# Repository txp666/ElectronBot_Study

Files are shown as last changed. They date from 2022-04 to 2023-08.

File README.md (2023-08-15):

**资料下载：**

链接: https://pan.baidu.com/s/1p0newnkKFVqm6W-avRse6w?pwd=cxn6 提取码: cxn6 复制这段内容后打开百度网盘手机App，操作更方便哦

QQ群：147597938

ElectronBot_Unity压缩包是补充了dll的unity上位机 来自群文件 感谢群友的分享！

| 值 | 封装 | 数量 | 分类 | 备注 |
| --- | --- | ---- | --- | :---: |
| 2.2nF | CAP_0402 | 1 | 电容电阻 | 阻容立创商城或者优信电子买 |
| 10nF | CAP_0402 | 10 | | |
| 0.1uF | CAP_0402 | 31 | | |
| 10uF | CAP_0402 | 17 | | |
| 0R | RES_0402 | 3 | | |
| 4.7R | RES_0402 | 1 | | |
| 10R | RES_0402 | 1 | | |
| 120R | RES_0402 | 6 | | |
| 200R | RES_0402 | 1 | | |
| 5.1K | RES_0402 | 2 | | |
| 10K | RES_0402 | 13 | | |
| 12K | RES_0402 | 1 | | |
| 47K | RES_0402 | 5 | | |
| 100K | RES_0402 | 1 | | |
| 1M | RES_0402 | 1 | | |
| [24MHz](https://item.taobao.com/item.htm?spm=a1z09.2.0.0.1f3c2e8df9Af9i&id=569633363622&_u=b20q7cgb7b7b) | 晶振-3P | 1 | 晶振 | |
| [8MHz](https://item.taobao.com/item.htm?spm=a1z09.2.0.0.1f3c2e8df9Af9i&id=569633363622&_u=b20q7cgb7b7b) | 晶振-3P | 1 | | |
| [CP2102](https://item.taobao.com/item.htm?spm=a1z10.3-c-s.w4002-21223910208.11.38616a4bJvtoO5&id=522575454240) | QFN-28 | 1 | 芯片 | |
| [LP2992 3V3](https://item.taobao.com/item.htm?spm=a1z09.2.0.0.29ee2e8dahZw7u&id=559236610497&_u=s20q7cgb15f7) | SOT23-5 | 8 | | 已修改为XC6210B332MR 3.3V/0.7A 可以替换2992，电流增大 |
| [STM32F405RGT6](https://item.taobao.com/item.htm?id=522577756409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) | LQFP-64_N | 1 | | |
| [STM32F030F6](https://item.taobao.com/item.htm?spm=a1z0d.6639537.1997196601.14.6ce87484rl1x1l&id=522554611977) | TSSOP-20 | 6 | | |
| [USB3300-EZK-TR](https://item.taobao.com/item.htm?spm=a1z09.2.0.0.1f3c2e8df9Af9i&id=615706097828&_u=b20q7cgb7b9f) | QFN-32 | 1 | | |
| [HS8836A](https://detail.tmall.com/item.htm?id=622686776816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) | SO-16N | 1 | | |
| [MPU6050](https://item.taobao.com/item.htm?spm=a1z10.3-c-s.w4002-21223910208.13.12246a4bkkMiAU&id=522575310310) | QFN-24 | 1 | | 可以不买 |
| [PAJ7620U2](https://item.taobao.com/item.htm?spm=a1z09.2.0.0.1f3c2e8df9Af9i&id=571178228286&_u=b20q7cgb3b28) | PAJ7620U2 | 1 | | |
| [FM116B](https://item.taobao.com/item.htm?spm=a1z09.2.0.0.1f3c2e8df9Af9i&id=618979113359&_u=b20q7cgb4a9d) | SOT23-6 | 6 | | |
| [AO3400A](https://item.taobao.com/item.htm?spm=a1z10.3-c-s.w4002-21223910208.9.43706a4bLb8vCV&id=522574089119) | SOT23-3 | 1 | | |
| [TL431IDBZT](https://item.taobao.com/item.htm?spm=a1z09.2.0.0.67002e8dJ6XlJx&id=554339815306&_u=b20q7cgbc675) | SOT23-3 | 6 | | |
| [Type-C](https://item.taobao.com/item.htm?spm=a1z09.2.0.0.62442e8demH03x&id=573090887123&_u=g20q7cgb5a83) | | 1 | 连接件 | |
| [FFC_0.5_8](https://item.taobao.com/item.htm?spm=a1z09.2.0.0.62442e8dmareSl&id=552629356951&_u=g20q7cgb4b1f) | FFC_0.5_8 | 4 | | |
| [SH1.0-4P](https://item.taobao.com/item.htm?spm=a1z09.2.0.0.62442e8demH03x&id=565715285795&_u=g20q7cgbab7d) | SH1.0-4P | 10 | | 3 4 p都多买点5p是DK板的可以不买 |
| TF-Socket | TF-Card-Amphenol with TF | 1 | | 可以不买 |
| [LCD-240x240-ROUND](https://item.taobao.com/item.htm?spm=a210c.1.0.0.79791debq2j2F8&id=666438287702&qq-pf-to=pcqq.c2c) | GC9A01 | 1 | | |
| [表盘](https://item.taobao.com/item.htm?spm=a1z09.2.0.0.1f3c2e8df9Af9i&id=624702562166&_u=b20q7cgb2244) | 31.5mm | 1 | | |
| [摄像头](https://item.taobao.com/item.htm?spm=a1z09.2.0.0.1f3c2e8df9Af9i&id=567717780577&_u=b20q7cgb6b84) | usb摄像头 | 1 | | |
| [FFC排线](https://item.taobao.com/item.htm?spm=a1z09.2.0.0.5cf62e8dtZRRxc&id=549590794021&_u=p20q7cgb7a40) | 0.5*8 | 10 | | 同向反向都买点，10cm |
| [4.3g舵机](https://item.taobao.com/item.htm?spm=a1z09.2.0.0.1f3c2e8df9Af9i&id=601889539677&_u=b20q7cgb34d4) | | 5 | | |
| [9g舵机](https://item.taobao.com/item.htm?spm=a1z09.2.0.0.5cf62e8dtZRRxc&id=577455964879&_u=p20q7cgb27e6) | | 1 | | |
| [SH1.0 4p线](https://item.taobao.com/item.htm?spm=a1z09.2.0.0.62442e8demH03x&id=565360096163&_u=g20q7cgb107d) | | 6 | | 3 4 p都买点 5p是DK板的可以不买 |
| [推杆](https://item.taobao.com/item.htm?spm=a1z09.2.0.0.1f3c2e8df9Af9i&id=597058278501&_u=b20q7cgb396b) | M2*25 | 2 | | |
| [轴承](https://item.taobao.com/item.htm?spm=a1z09.2.0.0.1f3c2e8df9Af9i&id=550670695721&_u=b20q7cgbace2) [轴承](https://item.taobao.com/item.htm?spm=a1z09.2.0.0.1f3c2e8df9Af9i&id=626925470285&_u=b20q7cgbb95a) | 肩膀6x10x3mm 腰部25x32x4mm | | | 内径25外径32高度4 |
| [螺丝](https://item.taobao.com/item.htm?spm=a1z09.2.0.0.1f3c2e8df9Af9i&id=571154046536&_u=b20q7cgb74bb) | M2 | 若干 | | 螺丝挑几个M2*4,5,6的买点就行，我图方便买了一盒 |
| [m1*10](https://item.taobao.com/item.htm?spm=a1z09.2.0.0.98452e8dyw0XaE&id=591244120254&_u=m20q7cgb4fc2) | 舵机拆后壳后固定 | 12 | | |

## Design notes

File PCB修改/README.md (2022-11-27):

# [立创EDA工程已同步](https://oshwhub.com/txp666/electronbot_study)

## 2022/11/26更新

主板电阻电容增大间距，不易连锡；

CP2102兼容了[CH9102X](https://item.taobao.com/item.htm?spm=a230r.1.14.6.1bea68c9lNiSzG&id=675981384914&ns=1&abbucket=11#detail) 这个便宜一点；如果装CP2102左下角的0.1UF可不焊。

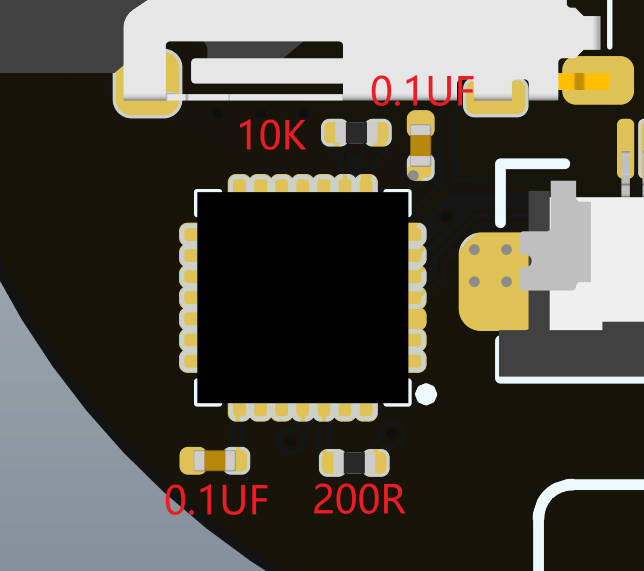
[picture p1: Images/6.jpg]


ServoDrive：

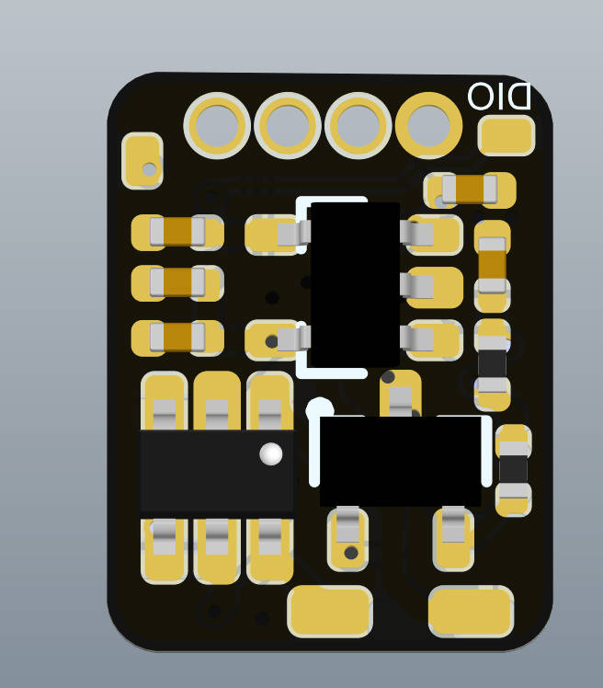
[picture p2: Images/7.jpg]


增加SensorBoardConnecter和ServoDriveConnecter 可以将舵机转FPC连接  （可选项，不需要打也行）



# 2022/7/24更新

ServoDrive增加5v入口10uF电容焊盘  有效解决舵机断联问题

微信截图_20220724125115

********************************************************************************************************************

ServoDrive 增大了烧录焊盘 和 4p连接线焊盘

ElectronBot主板把焊盘上的过孔移到焊盘外了、3300好焊很多

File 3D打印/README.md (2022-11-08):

# 3D打印

## 修改说明：

1、**PLUS版区别: **身体加宽1cm，更好安装，为了协调底座也加宽了

2、齿轮扩孔，可直接套上舵机自带的摇臂，并且齿轮与推杆舵机摇臂6合1，打印一份即可，省钱（推荐尼龙打印）

3、头部加了swd下载孔，方便调试

4、手臂推杆轴4in1 原版尺寸太小嘉立创不给打

5、肩部转轴2in1

6、底座下盖添加9g舵机摇臂安装位置（也需要螺丝固定），原版时间长了会打滑

## 2022/5/31：

齿轮组合与肩部转轴升级   更换了齿轮与肩轴连接方式不会空转



## 2022/9/1：

肩部转轴中心的孔扩大

手臂螺丝孔缩小

## 2022/11/5：

内侧删掉了突起

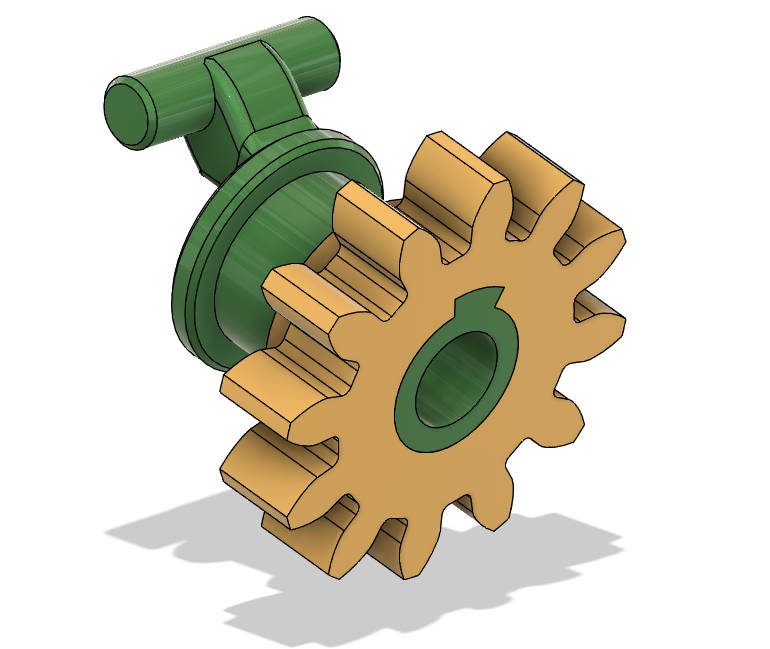
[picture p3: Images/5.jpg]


## 2022/11/8:

齿轮组合中的舵机摇臂尺寸修正，推杆更顺滑

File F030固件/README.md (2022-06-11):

**重要**：

***<u>在舵机控制板lp2992的5v入口放一个10uf电容，防止出现舵机失联</u>***

这些是舵机对应的f030f4p6对应的固件，烧录即可，不需要重新调试设置id

测试舵机是否正常工作：将main.cpp复制到f4主控的clion工程替换，更改n

n=1-6 对应 id 2~12

**PS**：如果舵机没反应，将f030芯片全部擦除再刷即可（烧录工具有个橡皮擦）

**PS**: 上位机体调试的时候，如果舵机转动方向与上位机中的不一样，调换电机线，同时调换电位器正反（adc以外的两条）即可

id

**注意**stlinkUtility连接舵机板设置如下

屏幕截图 2022-05-20 202718

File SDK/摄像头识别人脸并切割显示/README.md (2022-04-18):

在lowlevel中替换sample.cpp

把NoFace.jpg放入工程根目录

vs环境请参考视频https://www.bilibili.com/video/BV1zq4y1a7r4?share_source=copy_web

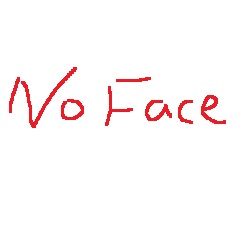
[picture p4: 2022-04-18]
SDK/摄像头识别人脸并切割显示/NoFace.jpg

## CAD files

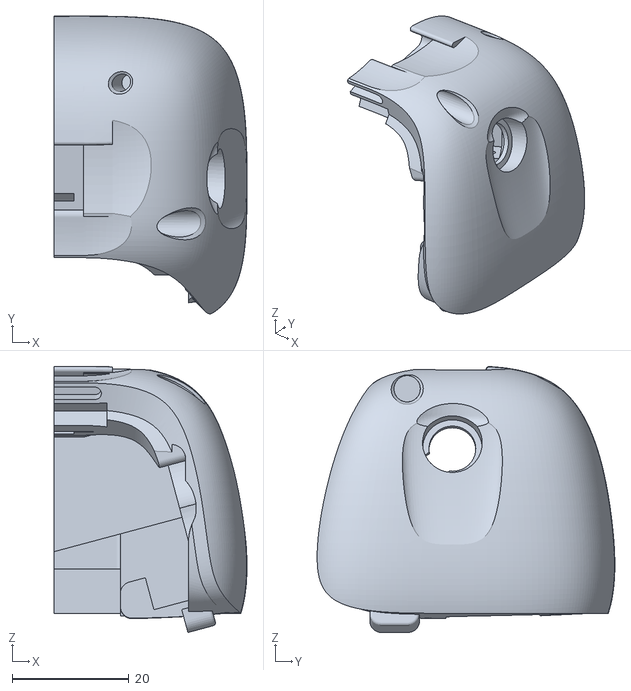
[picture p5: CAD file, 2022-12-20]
3D打印/PLUS(胖)/身体后壳-左 .stl
33.0 x 50.9 x 45.5

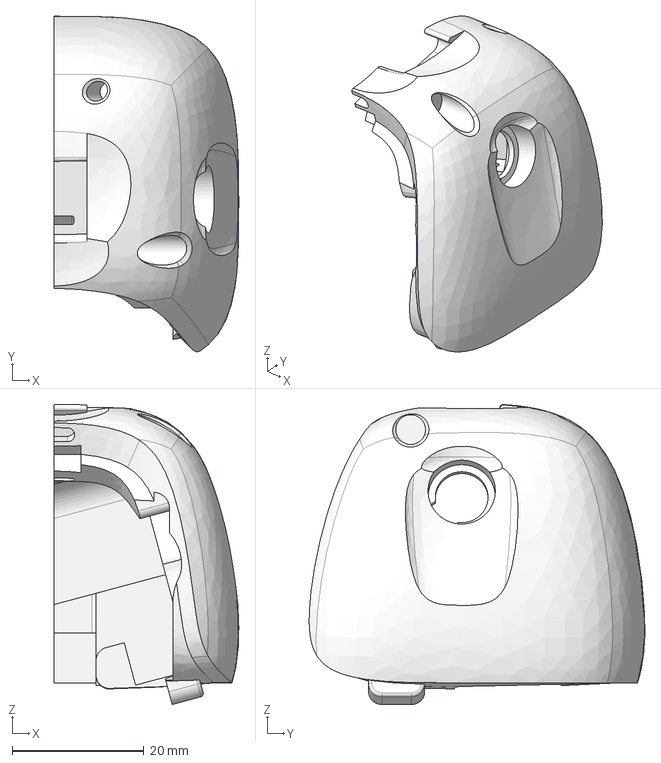
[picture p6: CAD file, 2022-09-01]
3D打印/原版-修改部分细节/身体后壳-左.step
28.0 x 50.9 x 45.5 mm

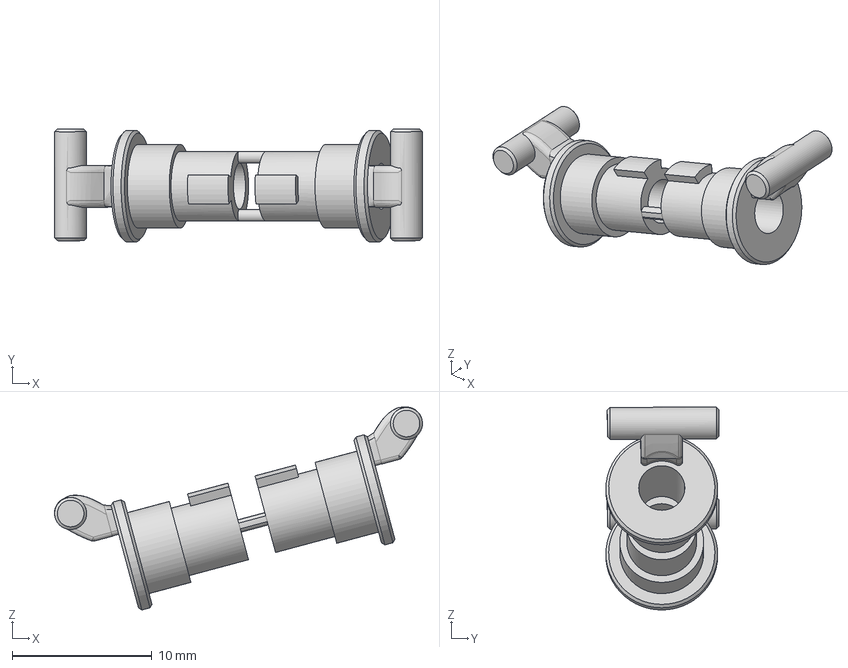
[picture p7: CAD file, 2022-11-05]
3D打印/PLUS(胖)/肩部转轴(2in1)(尼龙) v3.step
26.3 x 8.11 x 14.5 mm

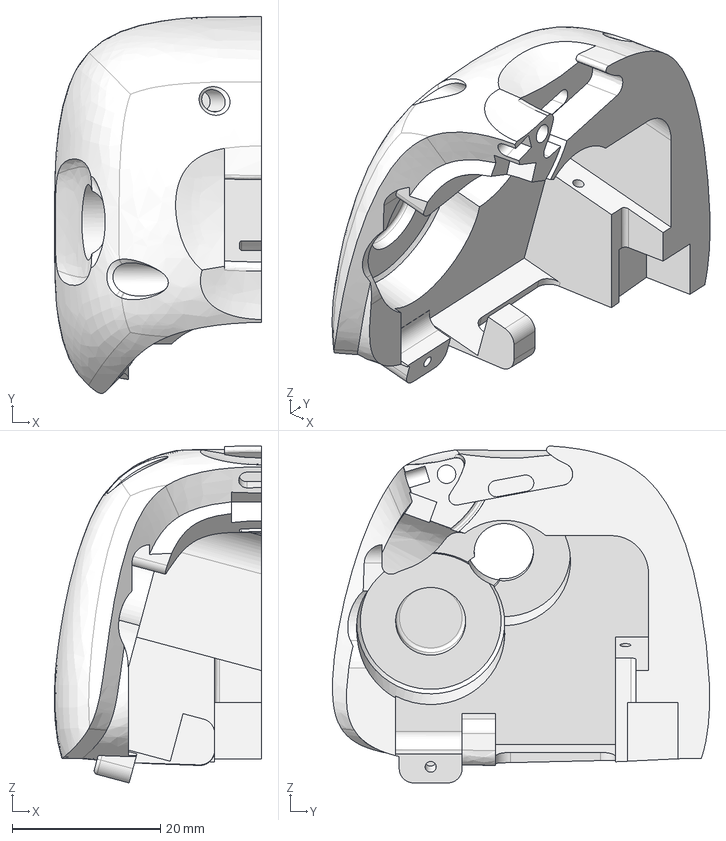
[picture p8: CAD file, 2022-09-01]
3D打印/原版-修改部分细节/身体后壳-右 .step
28.0 x 50.9 x 45.5 mm

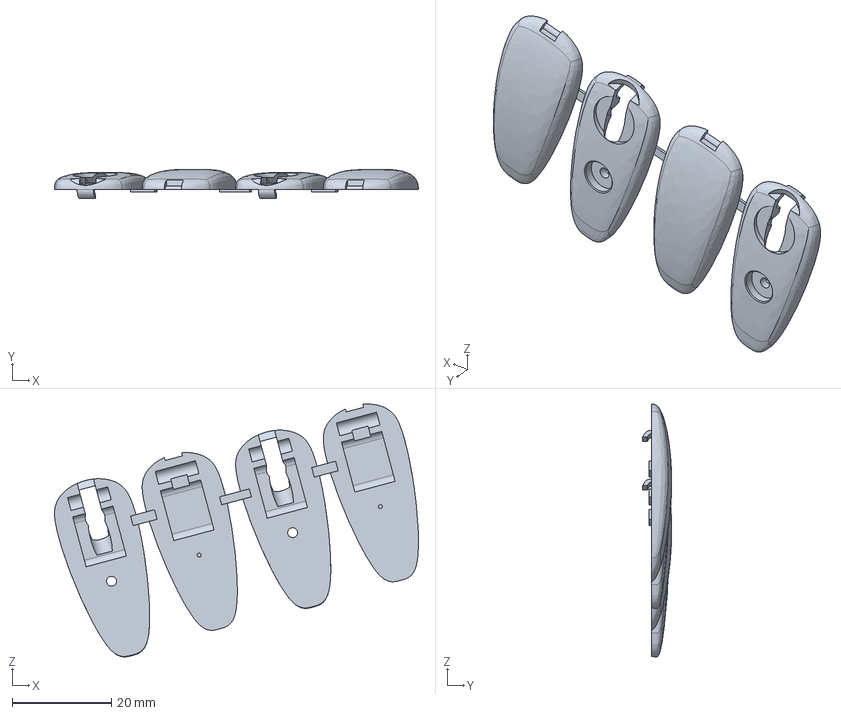
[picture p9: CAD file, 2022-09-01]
3D打印/PLUS(胖)/手臂4in1.step
73.4 x 5.94 x 51.0 mm

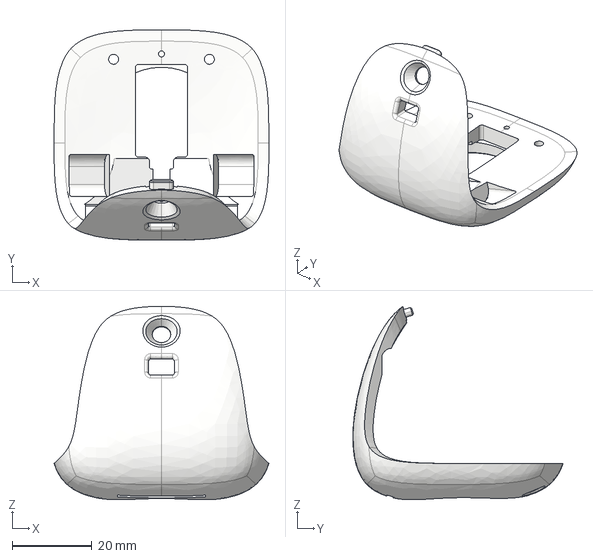
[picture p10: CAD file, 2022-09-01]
3D打印/原版-修改部分细节/身体前部.step
53.9 x 52.7 x 48.5 mm

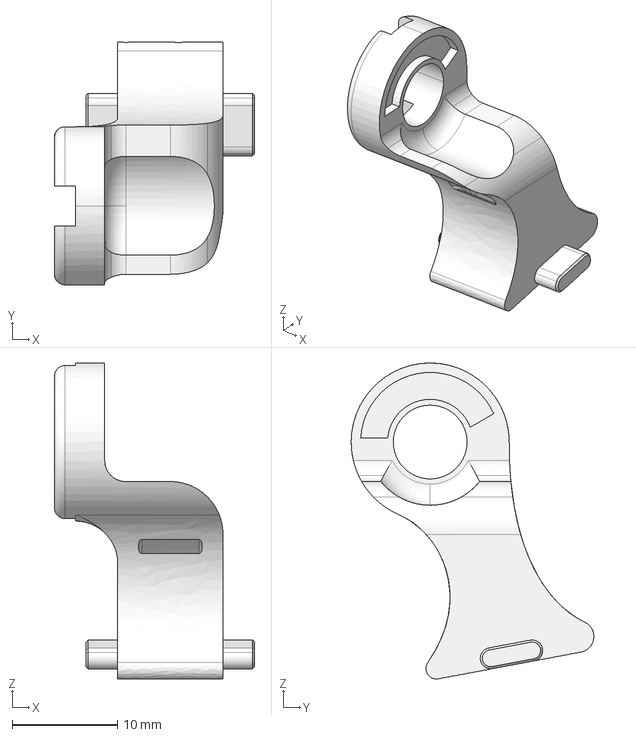
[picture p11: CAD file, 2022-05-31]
3D打印/PLUS(胖)/颈部.step
19.0 x 23.0 x 30.0 mm

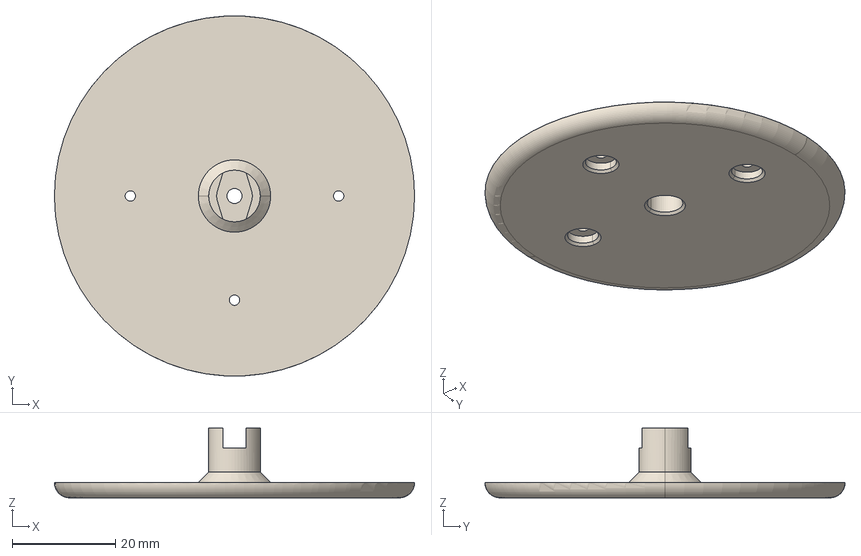
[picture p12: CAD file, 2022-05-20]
3D打印/PLUS(胖)/底座下盖.step
69.7 x 69.7 x 13.5 mm

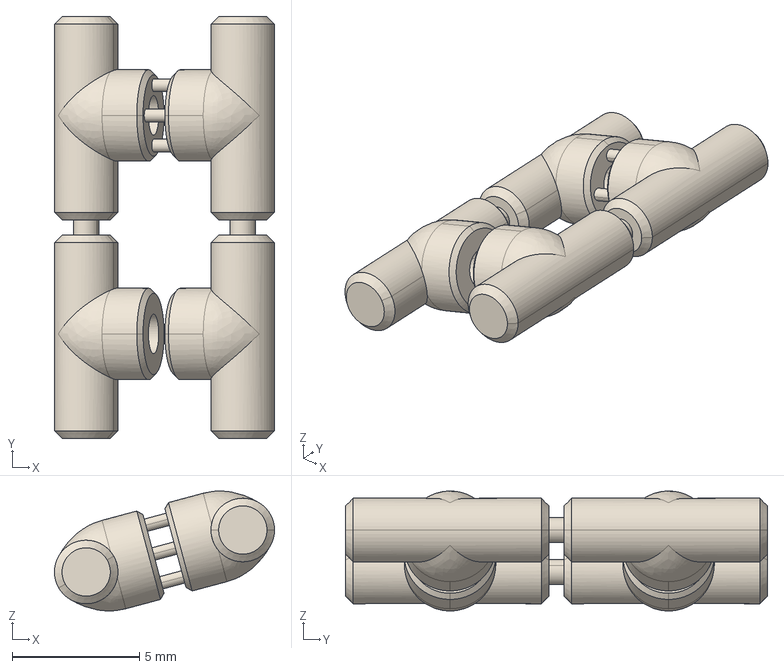
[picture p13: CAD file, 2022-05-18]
3D打印/PLUS(胖)/手臂推杆轴.step
8.66 x 16.6 x 4.71 mm

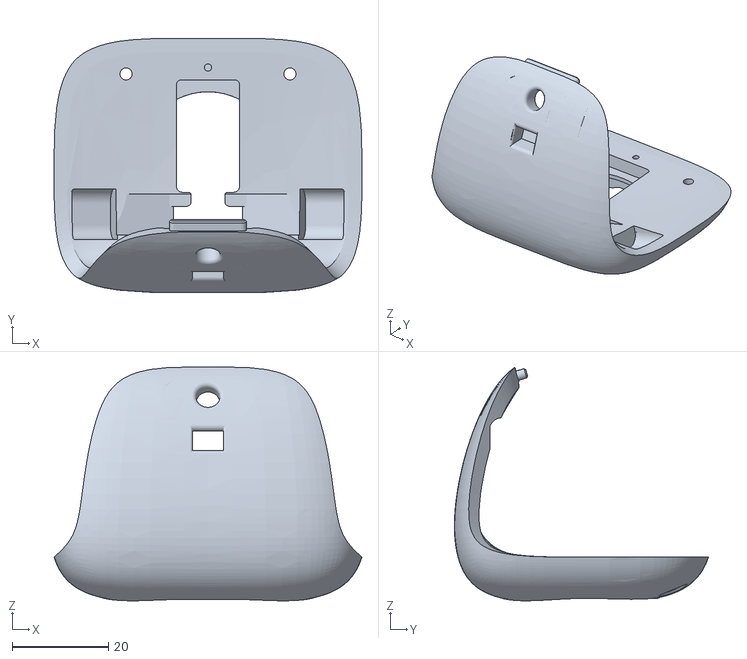
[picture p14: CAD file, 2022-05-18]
3D打印/PLUS(胖)/身体前壳.stl
63.9 x 52.7 x 48.5

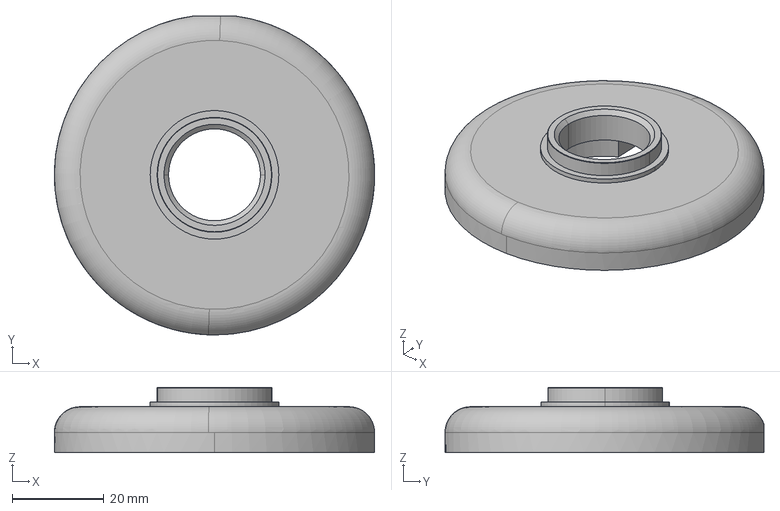
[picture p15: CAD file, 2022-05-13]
3D打印/PLUS(胖)/底座上盖.step
69.7 x 69.4 x 14.2 mm

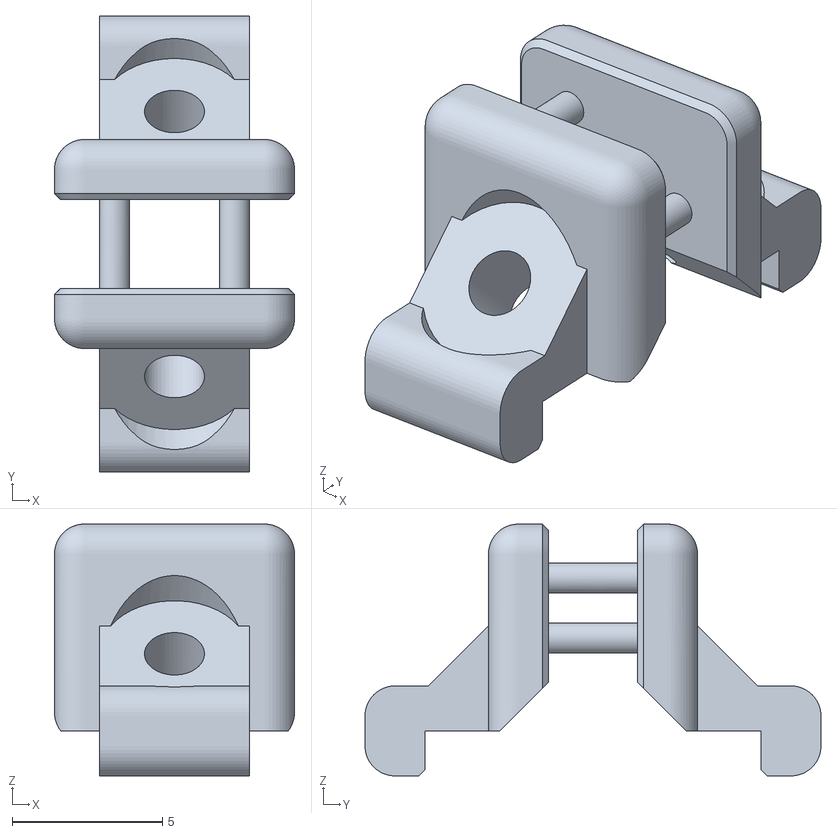
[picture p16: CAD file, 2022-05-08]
3D打印/PLUS(胖)/控制板固定件2in1.stl
8.00 x 15.2 x 8.39

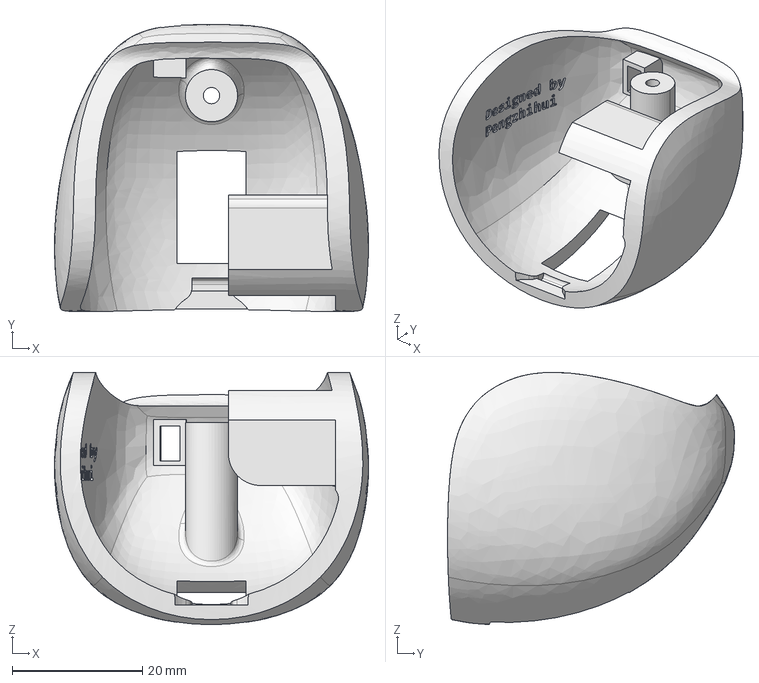
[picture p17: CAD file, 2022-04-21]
3D打印/PLUS(胖)/头部后壳.step
48.2 x 44.1 x 38.7 mm

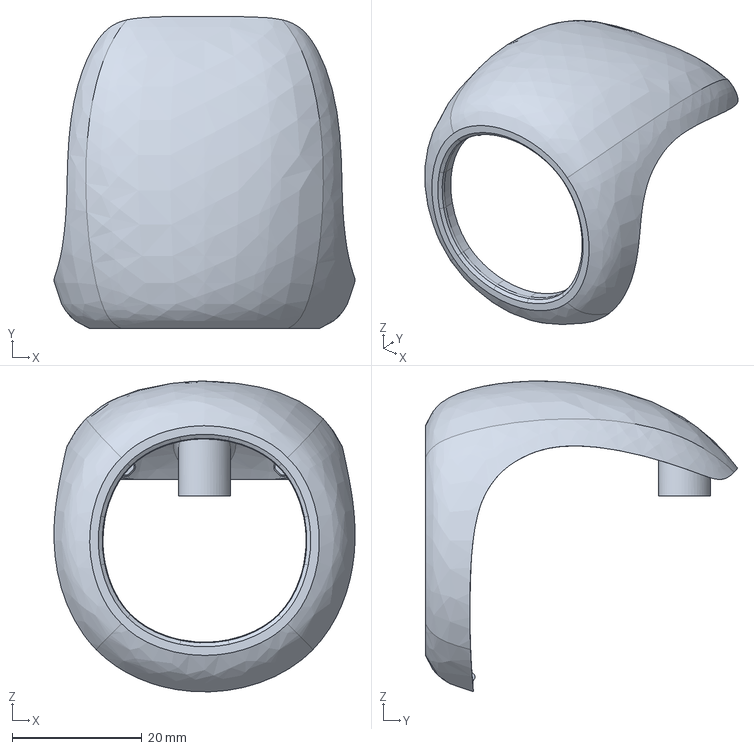
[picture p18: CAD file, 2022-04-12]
3D打印/PLUS(胖)/头部前壳.step
46.4 x 48.2 x 47.9 mm

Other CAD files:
3D打印/PLUS(胖)/身体后壳_右.stl

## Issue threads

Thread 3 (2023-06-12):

HS8836A 那家店买到的是坏的（也可能是概率），建议更新为群里的 BOM 表上的店

smileorigin, 2023-06-12:
如题，不然容易让新手小白找不到问题在哪里，还是比较麻烦的

txp666, 2023-08-09:
坏的概率小吧，我买了不少没坏的

txp666, 2023-08-15:
ok 已更新

Closed 2023-08-15.

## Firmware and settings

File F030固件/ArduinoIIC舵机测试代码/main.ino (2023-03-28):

#include "robot.h"

Robot electron;

void setup()
{
  Wire.begin(8, 9); //sda 8,scl 9
  delay(2000);
  Serial.begin(115200);

}

void loop()
{

  int n =1;   //1-6
  electron.joint[n].angleMin = 0;
  electron.joint[n].angleMax = 180;
  electron.joint[n].angle = 0;
  electron.joint[n].modelAngelMin = -90;
  electron.joint[n].modelAngelMax = 90;
  electron.SetJointEnable(electron.joint[n], true);

  for (int i = -90; i < 90; i += 1)
  {
    float angle = i;
    electron.UpdateJointAngle(electron.joint[n], angle);

    delay(20);
  }
  for (int i = 90; i > -90; i -= 1)
  {
    float angle = i;
    electron.UpdateJointAngle(electron.joint[n], angle);

    delay(20);
  }
}

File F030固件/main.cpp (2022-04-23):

#include <cmath>
#include "common_inc.h"
#include "screen.h"
#include "robot.h"


Robot electron(&hspi1, &hi2c1);
float jointSetPoints[6];
bool isEnabled = false;
/* Thread Definitions -----------------------------------------------------*/

/* Timer Callbacks -------------------------------------------------------*/


/* Default Entry -------------------------------------------------------*/

void Main(void)
{

    HAL_Delay(2000);
    electron.lcd->Init(Screen::DEGREE_0);
    electron.lcd->SetWindow(0, 239, 0, 239);

    int n=6;
    electron.joint[n].angleMin = 0;
    electron.joint[n].angleMax = 180;
    electron.joint[n].angle = 0;
    electron.joint[n].modelAngelMin = -90;
    electron.joint[n].modelAngelMax = 90;
    electron.SetJointEnable(electron.joint[n], true);

    while (1)
    {
        for (int i = -90; i < 90; i += 1)
        {
            float angle = i;
            electron.UpdateJointAngle(electron.joint[n], angle);

            HAL_Delay(20);
        }
        for (int i = 90; i > -90; i -= 1)
        {
            float angle = i;
            electron.UpdateJointAngle(electron.joint[n], angle);

            HAL_Delay(20);
        }
    }

}



extern "C"
void HAL_SPI_TxCpltCallback(SPI_HandleTypeDef* hspi)
{
    electron.lcd->isBusy = false;
}

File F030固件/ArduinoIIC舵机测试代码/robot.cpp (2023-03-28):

#include "robot.h"

void Robot::UpdateServoAngle(Robot::JointStatus_t &_joint, float _angleSetPoint)
{
    if (_angleSetPoint >= _joint.angleMin && _angleSetPoint <= _joint.angleMax)
    {
        auto *b = (unsigned char *)(&_angleSetPoint);

        i2cTxData[0] = 0x01;
        for (int i = 0; i < 4; i++)
            i2cTxData[i + 1] = *(b + i);

        TransmitAndReceiveI2cPacket(_joint.id);

        _joint.angle = *(float *)(i2cRxData + 1);
    }
}

void Robot::UpdateServoAngle(Robot::JointStatus_t &_joint)
{
    auto *b = (unsigned char *)&(_joint.angle);

    i2cTxData[0] = 0x11;

    TransmitAndReceiveI2cPacket(_joint.id);

    _joint.angle = *(float *)(i2cRxData + 1);
}

void Robot::SetJointEnable(Robot::JointStatus_t &_joint, bool _enable)
{
    i2cTxData[0] = 0xff;
    i2cTxData[1] = _enable ? 1 : 0;

    TransmitAndReceiveI2cPacket(_joint.id);

    _joint.angle = *(float *)(i2cRxData + 1);
}

void Robot::TransmitAndReceiveI2cPacket(uint8_t _id)
{
    // 发送数据
    Wire.beginTransmission(_id);
    for (int i = 0; i < 5; i++)
    {
        Wire.write(i2cTxData[i]);
    }
    byte txError = Wire.endTransmission();
    while (txError != 0)
    {
        delay(5); // 重试间隔
        Wire.beginTransmission(_id);
        for (int i = 0; i < 5; i++)
        {
            Wire.write(i2cTxData[i]);
        }
        txError = Wire.endTransmission();
    }

    // 接收数据
    byte bytesRead = 0;
    while (bytesRead != 5)
    {
        bytesRead = Wire.requestFrom(_id, 5);
        delay(5); // 重试间隔
    }

    for (int i = 0; i < bytesRead; i++)
    {
        i2cRxData[i] = Wire.read();
    }
}



void Robot::SetJointTorqueLimit(Robot::JointStatus_t &_joint, float _percent)
{
    if (_percent >= 0 && _percent <= 1)
    {
        auto *b = (unsigned char *)(&_percent);

        i2cTxData[0] = 0x26;
        for (int i = 0; i < 4; i++)
            i2cTxData[i + 1] = *(b + i);

        TransmitAndReceiveI2cPacket(_joint.id);

        _joint.angle = *(float *)(i2cRxData + 1);

        delay(500); // wait servo reset
    }
}

void Robot::SetJointId(Robot::JointStatus_t &_joint, uint8_t _id)
{
    i2cTxData[0] = 0x21;
    i2cTxData[1] = _id;

    TransmitAndReceiveI2cPacket(_joint.id);

    _joint.angle = *(float *)(i2cRxData + 1);

    delay(500); // wait servo reset
}

void Robot::SetJointInitAngle(Robot::JointStatus_t &_joint, float _angle)
{
    float sAngle = _joint.inverted ? (_angle - _joint.modelAngelMin) /
                                             (_joint.modelAngelMax - _joint.modelAngelMin) *
                                             (_joint.angleMin - _joint.angleMax) +
                                         _joint.angleMax
                                   : (_angle - _joint.modelAngelMin) /
                                             (_joint.modelAngelMax - _joint.modelAngelMin) *
                                             (_joint.angleMax - _joint.angleMin) +
                                         _joint.angleMin;

    if (sAngle >= _joint.angleMin && sAngle <= _joint.angleMax)
    {
        auto *b = (unsigned char *)(&_angle);

        i2cTxData[0] = 0x27;
        for (int i = 0; i < 4; i++)
            i2cTxData[i + 1] = *(b + i);

        TransmitAndReceiveI2cPacket(_joint.id);

        _joint.angle = *(float *)(i2cRxData + 1);

        delay(500); // wait servo reset
    }
}

void Robot::SetJointKp(Robot::JointStatus_t &_joint, float _value)
{
    auto *b = (unsigned char *)(&_value);

    i2cTxData[0] = 0x22;
    for (int i = 0; i < 4; i++)
        i2cTxData[i + 1] = *(b + i);

    TransmitAndReceiveI2cPacket(_joint.id);

    _joint.angle = *(float *)(i2cRxData + 1);

    delay(500); // wait servo reset
}

void Robot::SetJointKi(Robot::JointStatus_t &_joint, float _value)
{
    auto *b = (unsigned char *)(&_value);

    i2cTxData[0] = 0x23;
    for (int i = 0; i < 4; i++)
        i2cTxData[i + 1] = *(b + i);

    TransmitAndReceiveI2cPacket(_joint.id);

    _joint.angle = *(float *)(i2cRxData + 1);

    delay(500); // wait servo reset
}

void Robot::SetJointKv(Robot::JointStatus_t &_joint, float _value)
{
    auto *b = (unsigned char *)(&_value);

    i2cTxData[0] = 0x24;
    for (int i = 0; i < 4; i++)
        i2cTxData[i + 1] = *(b + i);

    TransmitAndReceiveI2cPacket(_joint.id);

    _joint.angle = *(float *)(i2cRxData + 1);

    delay(500); // wait servo reset
}

void Robot::SetJointKd(Robot::JointStatus_t &_joint, float _value)
{
    auto *b = (unsigned char *)(&_value);

    i2cTxData[0] = 0x25;
    for (int i = 0; i < 4; i++)
        i2cTxData[i + 1] = *(b + i);

    TransmitAndReceiveI2cPacket(_joint.id);

    _joint.angle = *(float *)(i2cRxData + 1);

    delay(500); // wait servo reset
}

void Robot::UpdateJointAngle(Robot::JointStatus_t &_joint)
{
    UpdateServoAngle(_joint);

    float jAngle = _joint.inverted ? (_joint.angleMax - _joint.angle) /
                                             (_joint.angleMax - _joint.angleMin) *
                                             (_joint.modelAngelMax - _joint.modelAngelMin) +
                                         _joint.modelAngelMin
                                   : (_joint.angle - _joint.angleMin) /
                                             (_joint.angleMax - _joint.angleMin) *
                                             (_joint.modelAngelMax - _joint.modelAngelMin) +
                                         _joint.modelAngelMin;

    _joint.angle = jAngle;
}

void Robot::UpdateJointAngle(Robot::JointStatus_t &_joint, float _angleSetPoint)
{
    float sAngle = _joint.inverted ? (_angleSetPoint - _joint.modelAngelMin) /
                                             (_joint.modelAngelMax - _joint.modelAngelMin) *
                                             (_joint.angleMin - _joint.angleMax) +
                                         _joint.angleMax
                                   : (_angleSetPoint - _joint.modelAngelMin) /
                                             (_joint.modelAngelMax - _joint.modelAngelMin) *
                                             (_joint.angleMax - _joint.angleMin) +
                                         _joint.angleMin;

    UpdateServoAngle(_joint, sAngle);

    float jAngle = _joint.inverted ? (_joint.angleMax - _joint.angle) /
                                             (_joint.angleMax - _joint.angleMin) *
                                             (_joint.modelAngelMax - _joint.modelAngelMin) +
                                         _joint.modelAngelMin
                                   : (_joint.angle - _joint.angleMin) /
                                             (_joint.angleMax - _joint.angleMin) *
                                             (_joint.modelAngelMax - _joint.modelAngelMin) +
                                         _joint.modelAngelMin;

    _joint.angle = jAngle;
}

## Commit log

2022-04-12 Create Unity_ElectronBoty.rar
    添加unity上位机
2022-04-12 调试舵机
2022-04-12 del 舵机固件
2022-04-12 ADD 3D Model
    [头部前壳.step, 头部后壳.step, 底座上盖.step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]
2022-04-17 Create 人脸切割
2022-04-21 ADD 立创链接
2022-04-21 3d打印
    [嘉立创打不了_手臂推杆轴X2.step, 手臂内壳X2.step, 手臂外壳X2.step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]
2022-05-08 plus版
    [嘉立创打不了_手臂推杆轴X2.step, 头部前壳.step, 头部后壳.step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]
2022-05-08 底座加宽
    [底座下盖.step, 改_底座上盖.step, 改_底座下盖.step]
2022-05-08 肩部转轴2in1
    [改_肩部转轴X2.step, 改_肩部转轴x1(2in1).step]
2022-05-14 id12 p增大
2022-05-16 4in1 自己合并的，原来有问题
    [改_手臂4in1.step]
2022-05-18 身体前壳网格优化，推杆轴更换连接方式
    身体前壳网格优化，推杆轴更换连接方式
    [改_手臂推杆轴.step, 改_手臂推杆轴V1.1.step, 改_身体前壳V1.1.stl]
2022-05-20 添加舵机摇臂安装位置
    [改_底座下盖.step, 改_底座下盖v1.1.step]
2022-05-23 主板过孔移到焊盘外
2022-05-31 model update
    [改_肩部转轴(2in1)（尼龙）.step, 改_肩部转轴(2in1)（尼龙）V1.1.step, 改_颈部.step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]
2022-06-11 舵机失联解决
2022-07-24 ADD 10uf焊盘
    ServoDrive增加10UF焊盘 解决舵机断联问题
2022-08-22 PCB update
    舵机板连接方式改FPC
    有可能会解决缝隙问题
    未验证
    [Main.SchDoc, SensorBoard.PcbDoc, SensorBoard.PrjPCB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]
2022-08-22 Gerber update
    [SensorBoard.GBL, SensorBoard.GBO, SensorBoard.GBP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]
2022-08-26 更新 README.md
2022-09-01 原尺寸仅修改细节版
    [头部后壳.step, 底座上盖.step, 底座下盖.step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]
2022-11-04 Add 4PFPC Connecter
    [ElectronBot.GBL, ElectronBot.GBO, ElectronBot.GBP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]
2022-11-05 肩部转轴调整
    [肩部转轴(2in1)(尼龙) v3.step, 肩部转轴(2in1)（尼龙）.step, 齿轮组合（尼龙）.step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]
2022-11-05 更新 5.jpg
2022-11-08 推杆舵机摇臂尺寸修正，推杆更顺滑
2022-11-13 ADD SensorBoard Connecter
    [Connecter.PcbDoc, Main.SchDoc, SensorBoard.PcbDoc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]
2022-11-18 pcb add 滴泪
    [ServoDrive.PcbDoc, ServoDrive.PrjPCB]
2022-11-21 身体后壳右 填孔
    [身体后壳-左.step, 身体后壳_右.stl, 身体后壳_左.stl]
2022-11-26 pcb修改更新
    [Connecter.PcbDoc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]
2022-12-20 后壳左上传错误，已修正
    [身体后壳-左 .stl, 身体后壳-左.step]
2022-12-20 更新 身体后壳-左 .stl
    [身体后壳-左 .stl]
2023-03-28 Add Arduino IIC test
    移植舵机IIC控制到Arduino
2023-03-28 update Servo iic for Arduino
2023-03-28 更新 robot.h
2023-06-04 更新 底座上盖.step
    [底座上盖.step]
2023-08-15 删除原版
    [嘉立创打不了_手臂推杆轴X2.step, 头部前壳.step, 头部后壳.step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]
